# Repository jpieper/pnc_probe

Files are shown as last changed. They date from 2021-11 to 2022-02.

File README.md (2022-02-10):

# Pocket NC Probe Support #

This repository contains:

* Hardware designs to integrate a https://vers.by touch probe into the Pocket NC, https://pocketnc.com
* g-code routines for performing probe operations on the Pocket NC

# Usage #

When installed, [G38.x gcode commands](https://linuxcnc.org/docs/2.6/html/gcode/gcode.html#sec:G38-probe) work as expected.  If the jpieper/pnc_probe subroutines are installed, two new gcode programs are available: `pnc-probe-center-id` and `pnc-probe-center-od`.

These scripts probe features that are close to machine X=0,Y=0 and set G54 to the exact center.

To run either, manually position the probe along either the X axis or Y axis just inside (for ID) or just outside (for OD) at the depth you wish to probe.  Leave sufficient margin (~2mm) so that when the probe checks other directions it will have room to plunge without colliding with the work.

Then start the program.

# Installation #

## Hardware ##

Watch the following video:

TODO

1. Attach the adapter housing to the A axis stepper using a cable tie.  The cable tie should be pulled tight, as this helps keep the enclosure sealed from chips.

2. Disconnect the RJ45 cable from the A axis carriage and connect it to the bottom RJ45 port on the adapter.  The 1ft long ethernet cable should then be connected from the A axis carriage to the top port of the adapter.

3. To insert the probe, the A axis MUST be moved out of the home position.  Note, the machine CANNOT BE HOMED while the probe is inserted, or it will crash.

4. Using a dial indicator, adjust the M2 screws accessed through holes in the front of the probe to reduce runout at the tip of the probe.

5. Remove the screw cap from the adapter enclosure, attach the probe cable to the USB port.  Note, this is not actual USB, but that is the cable the vers.by ships with.

6. Attach the magnetic coupled end of the cable to the probe.

7. When removing the probe, be sure to reinstall the USB cap, otherwise chips may fall into the connector.

## Software ##

1. Copy the contents of the `ncfiles/` and `subroutines/` directories to `/home/pocketnc` on the pocketnc.  You can use WinSCP from Windows, or rsync from Mac/Linux.  A suitable command for linux might look like:

```
rsync -Pv ncfiles subroutines pocketnc@192.168.6.2:
```

2. Depending upon your machine version, you may need to add a .ini overlay.

### Kinetic ###

Modern versions of the Kinetic interface require no changes.

### Kinetic (pre 5.1.2) ###

Older versions of Kinetic require the following overlay added.

 * Config Tab
 * Server
 * INI OVERLAY
 * EDIT OVERLAY (bottom right)
 * If RS274NGC is not already in the list of groups, use the '+' button to add it.
 * Ensure the following key is set as follows:

```
SUBROUTINE_PATH=/opt/pocketnc/Settings/subroutines:/home/pocketnc/subroutines
```

 * If you had to change anything, click "REBOOT MACHINE".

### Legacy ###

TODO

# LICENSE #

All files contained in this repository are available under an Apache 2.0 License: https://www.apache.org/licenses/LICENSE-2.0

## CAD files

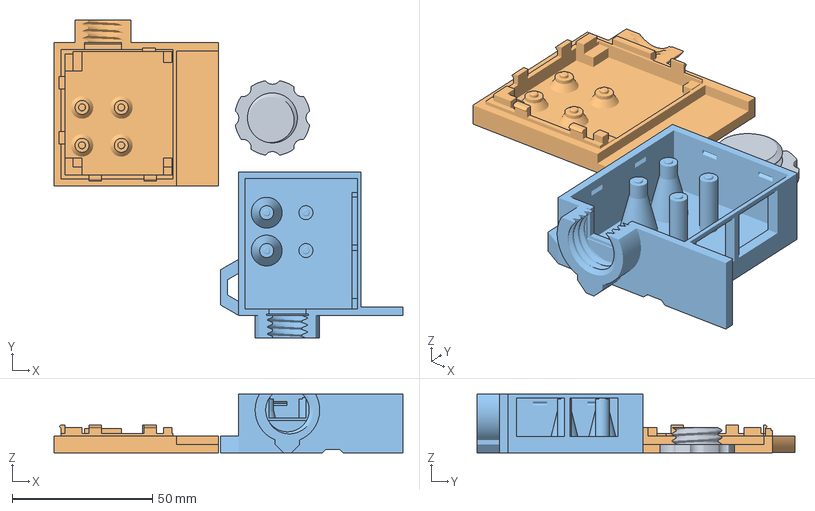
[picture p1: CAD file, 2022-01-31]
enclosure/pnc_probe_enclosure.3mf
124.4 x 113.3 x 21.0 mm
pnc_probe_usb_cap.stl
pnc_probe_enclosure_bottom.stl
pnc_probe_encosure_top.stl

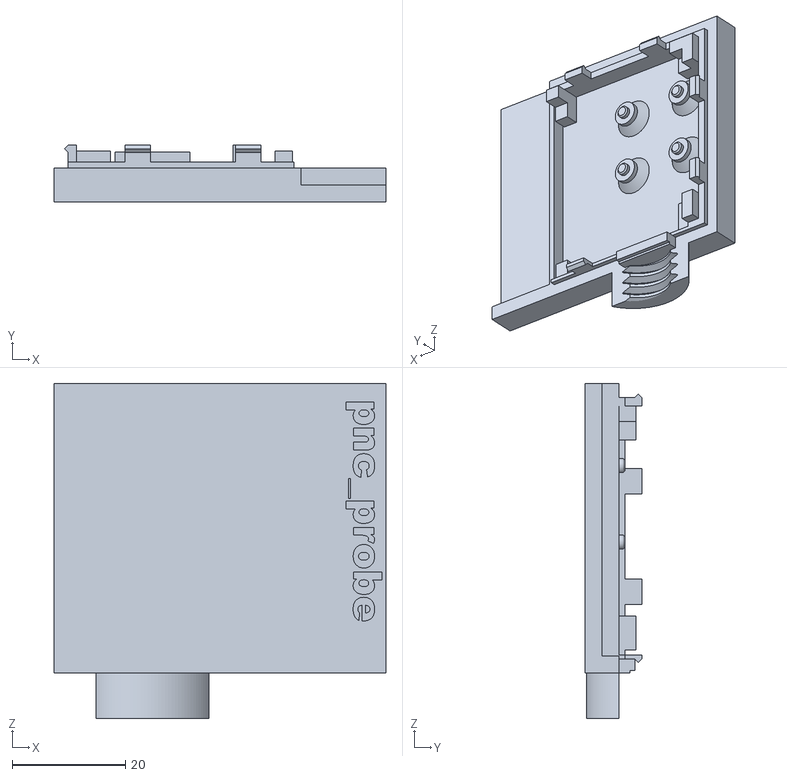
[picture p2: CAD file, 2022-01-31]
enclosure/pnc_probe_enclosure_bottom.stl
58.6 x 10.0 x 59.1

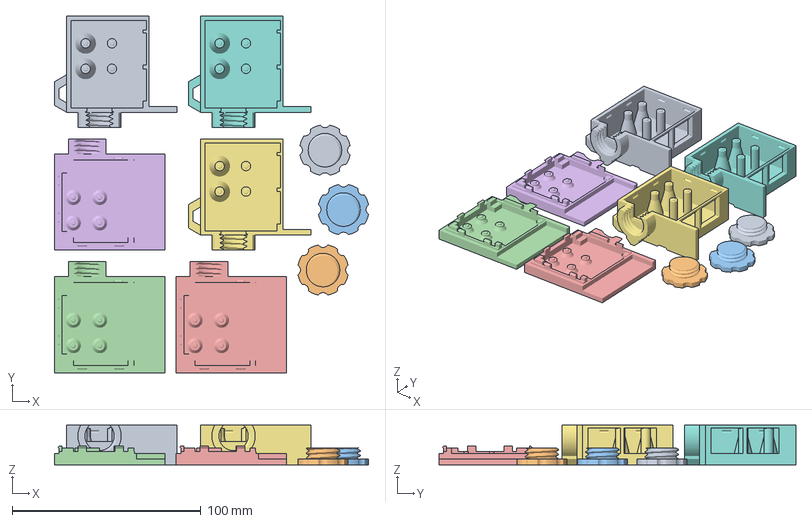
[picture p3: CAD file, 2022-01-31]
enclosure/pnc_probe_enclosure_3x_array.3mf
166.6 x 189.4 x 21.0 mm
pnc_probe_usb_cap.stl
pnc_probe_enclosure_bottom.stl
pnc_probe_encosure_top.stl

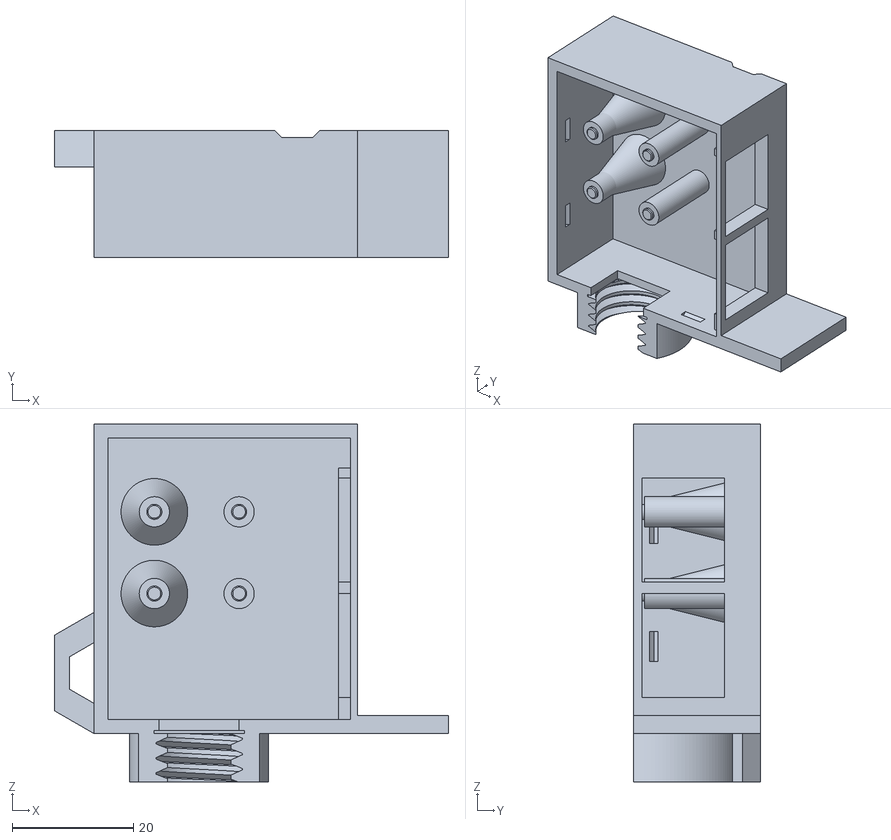
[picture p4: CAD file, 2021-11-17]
enclosure/pnc_probe_enclosure_top.stl
65.1 x 21.0 x 59.1

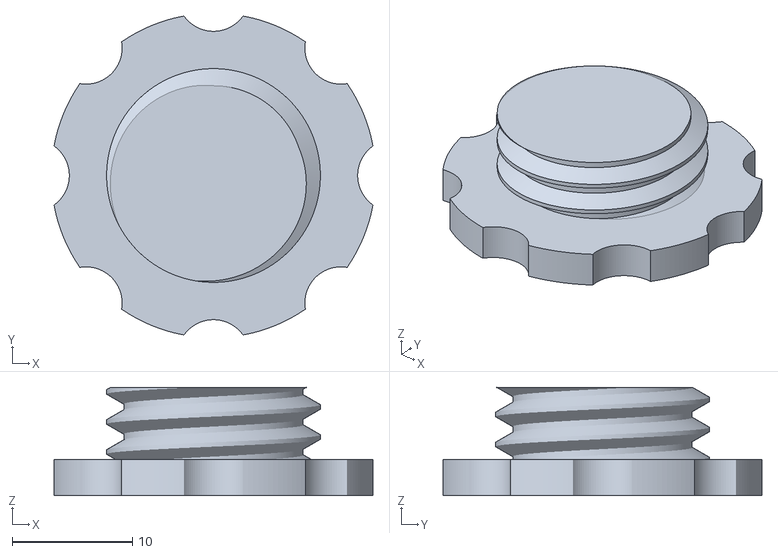
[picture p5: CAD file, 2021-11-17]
enclosure/pnc_probe_usb_cap.stl
26.6 x 26.6 x 9.00

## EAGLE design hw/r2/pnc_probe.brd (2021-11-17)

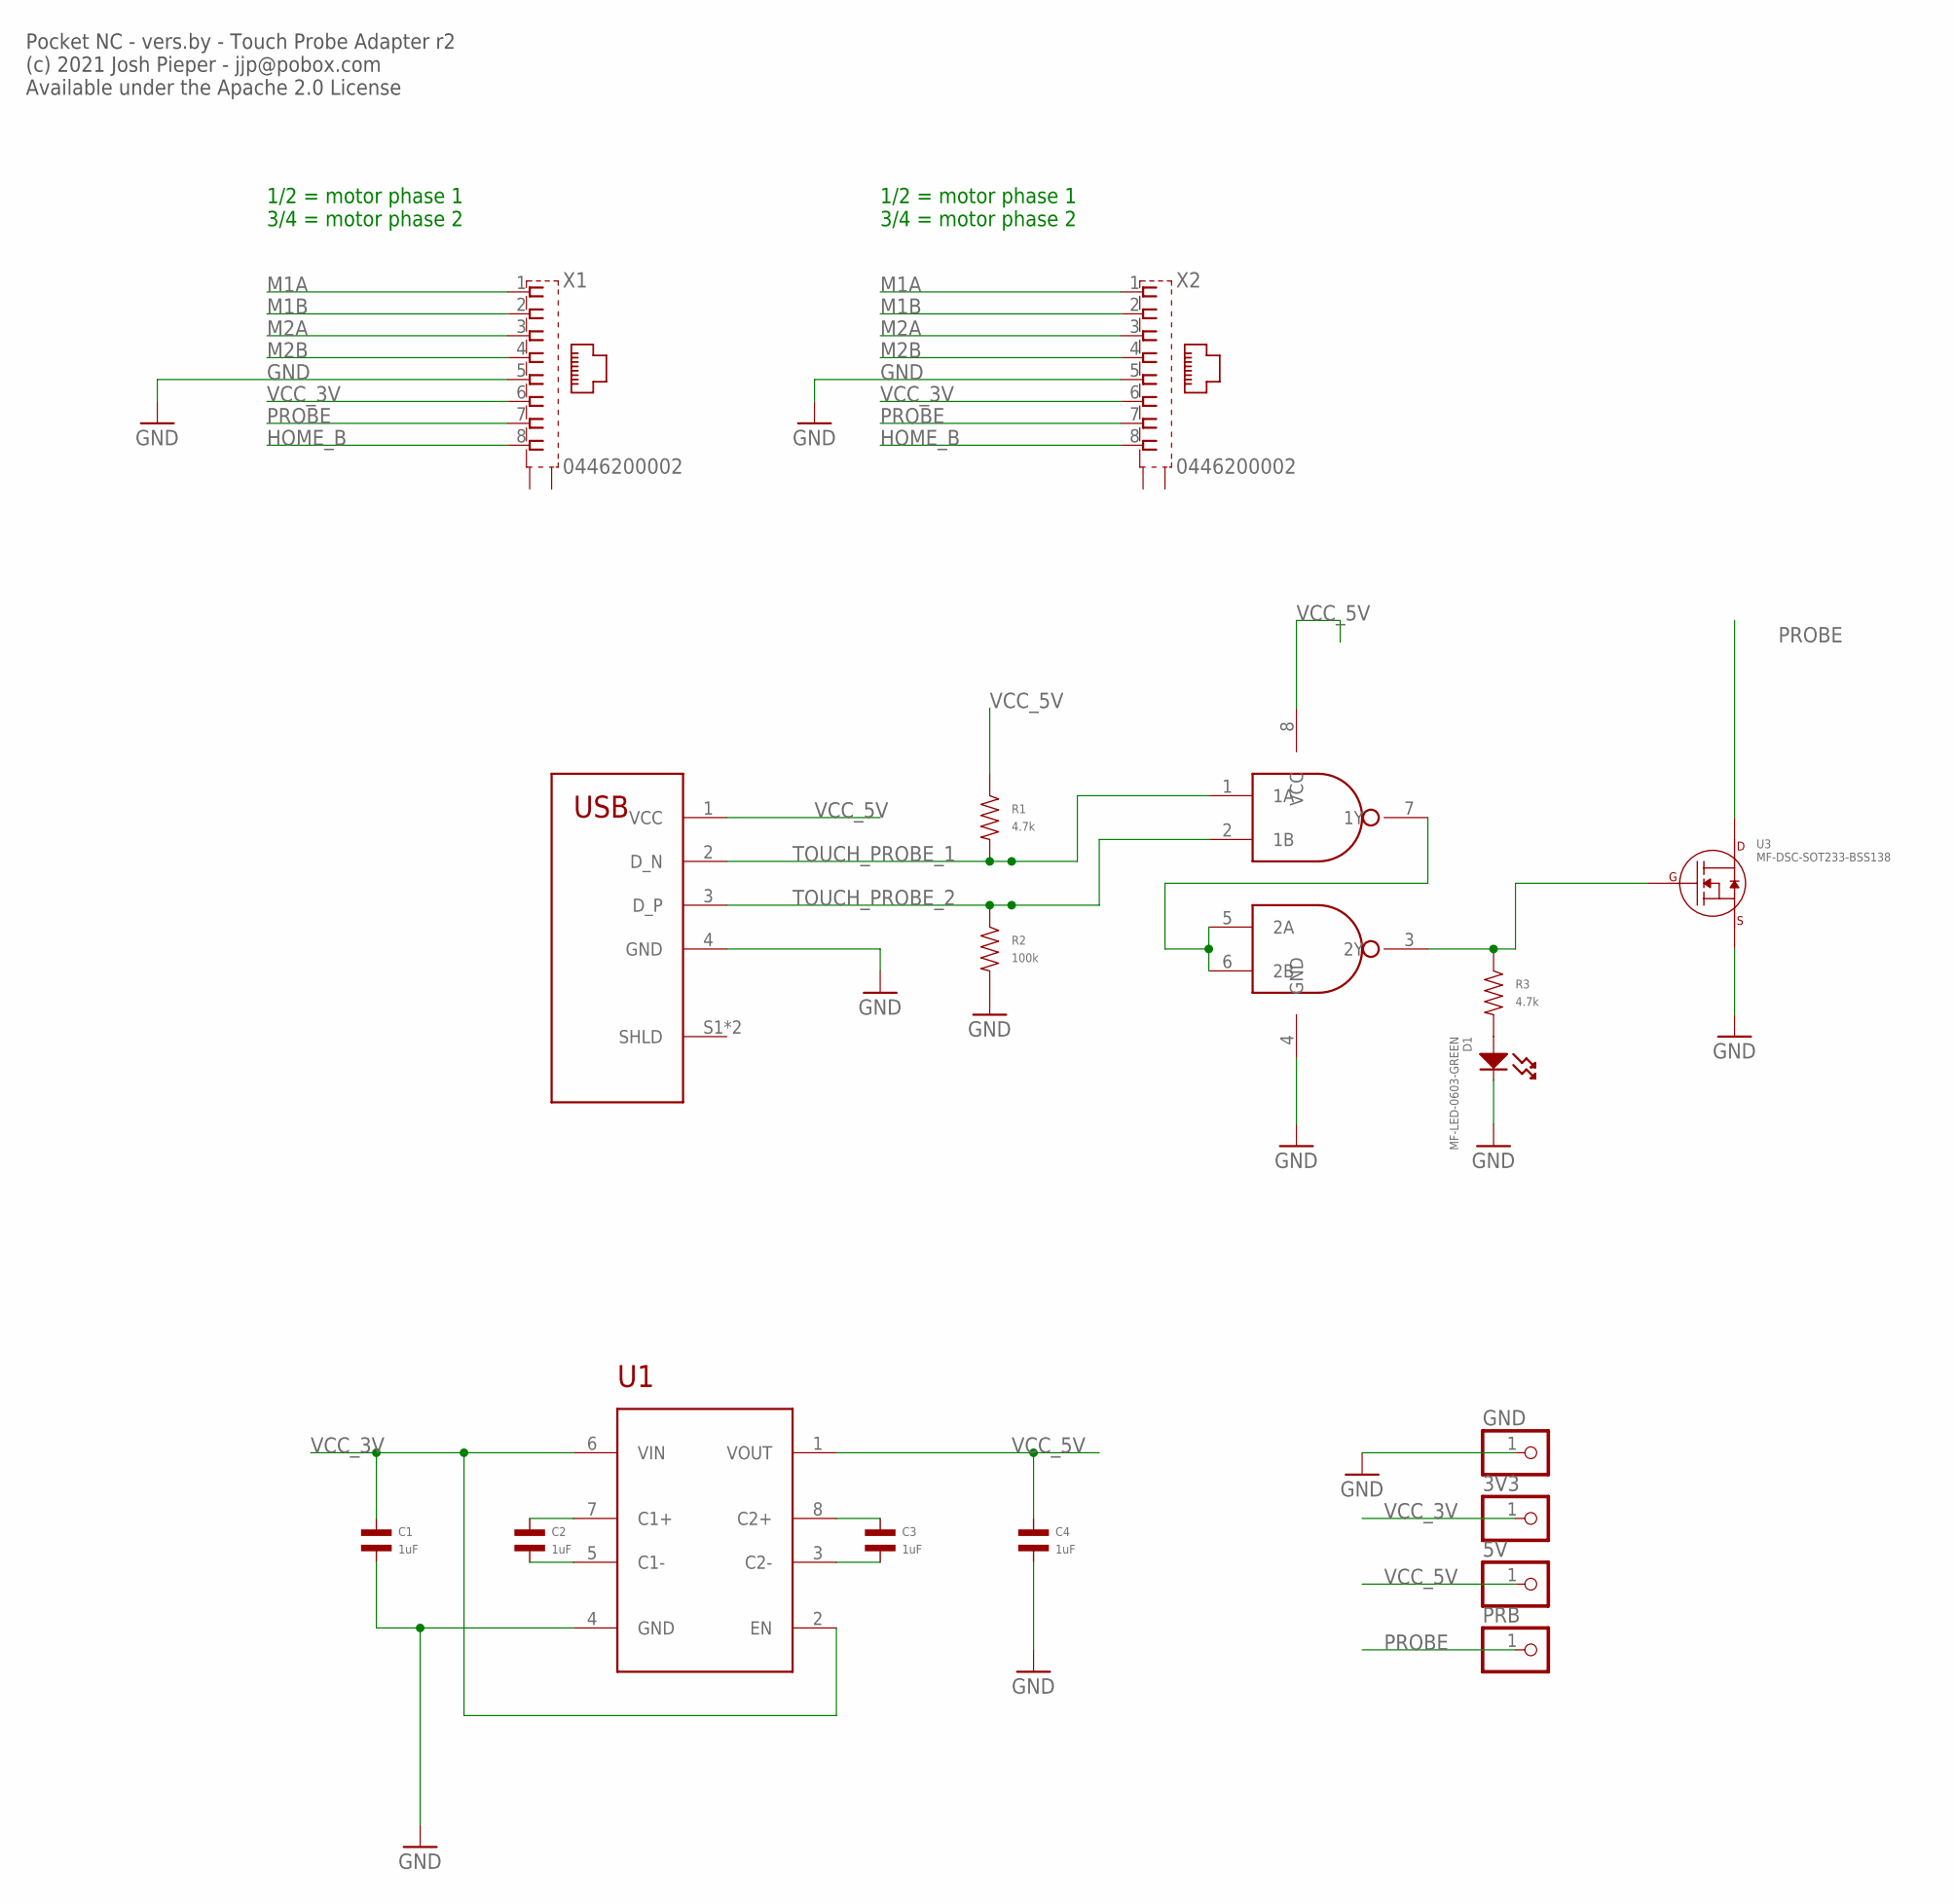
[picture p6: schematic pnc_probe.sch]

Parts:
3V3, 5V: PINHD-1X1; 1X01
C1, C2, C3, C4: 1uF; C0603; MPN MF-CAP-0603-1uF
D1: MF-LED-0603-GREEN; LED0603
GND: PINHD-1X1; 1X01
PRB: PINHD-1X1; 1X01
R1, R3: 4.7k; R0603; MPN MF-RES-0603-4.7K
R2: 100k; R0603; MPN MF-RES-0603-100K
U1: TPS6024X_VSSOP8; VSSOP8
U2: DUAL_NAND_SSOP8; SSOP8; MPN SN74LVC2G00DCTR
U3: MF-DSC-SOT233-BSS138; SOT-23-3
U$1: USBAUSBA; ONSHORE_USBA_1HSXX
X1, X2: 0446200002

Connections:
GND: C1.P$2, C4.P$2, D1.CATHODE, GND.1, R2.P$2, U1.4 (GND), U2.4 (GND), U3.P$2 (SOURCE), U$1.4 (GND), X1.5, X2.5
HOME_B: X1.8, X2.8
M1A: X1.1, X2.1
M1B: X1.2, X2.2
M2A: X1.3, X2.3
M2B: X1.4, X2.4
unnamed: U2.5 (2A), U2.6 (2B), U2.7 (1Y)
unnamed: C2.P$1, U1.7 (C1+)
unnamed: D1.ANODE, R3.P$2
unnamed: R3.P$1, U2.3 (2Y), U3.P$1 (GATE)
unnamed: C2.P$2, U1.5 (C1-)
unnamed: C3.P$1, U1.8 (C2+)
unnamed: C3.P$2, U1.3 (C2-)
PROBE: PRB.1, U3.P$3 (DRAIN), X1.7, X2.7
TOUCH_PROBE_1: R1.P$2, U2.1 (1A), U$1.2 (D_N)
TOUCH_PROBE_2: R2.P$1, U2.2 (1B), U$1.3 (D_P)
VCC_3V: 3V3.1, C1.P$1, U1.2 (EN), U1.6 (VIN), X1.6, X2.6
VCC_5V: 5V.1, C4.P$1, R1.P$1, U1.1 (VOUT), U2.8 (VCC), U$1.1 (VCC)

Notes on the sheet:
1/2 = motor phase 1 3/4 = motor phase 2
Pocket NC - vers.by - Touch Probe Adapter r2 (c) 2021 Josh Pieper - jjp@pobox.com Available under the Apache 2.0 License

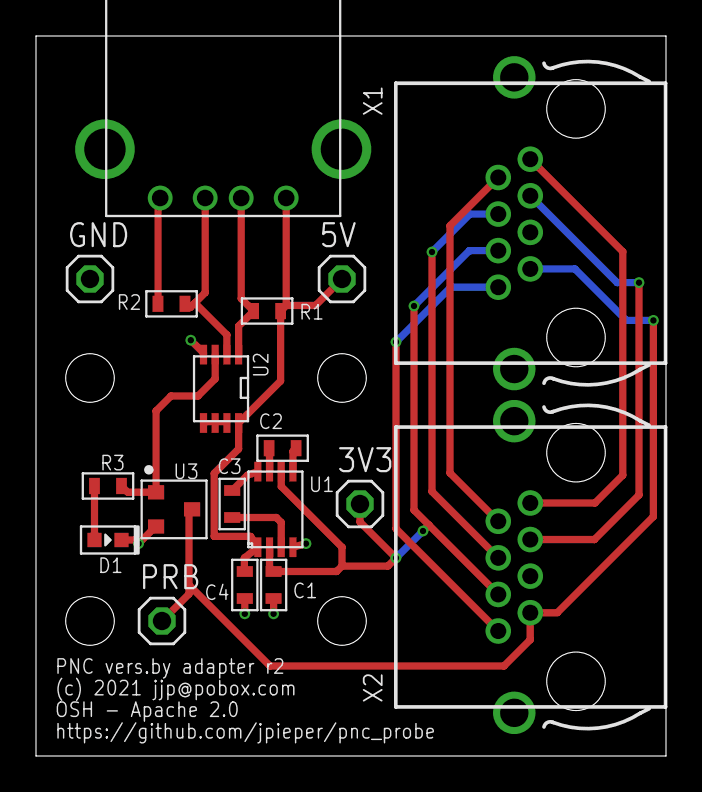
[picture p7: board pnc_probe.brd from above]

Board: 2 copper layers, 35.0 x 40.0 mm, 18 parts (0 on the bottom side), 18 nets.

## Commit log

2021-08-07 Draft of PCB
    [pnc_probe.brd, pnc_probe.sch]
2021-08-07 Random enclosure STLs
    [bottom.stl, enclosure.3mf, front.stl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]
2021-09-23 A script which probes the OD of a circle or square roughly already centered
2021-09-23 Fix r1 errata
    * The footprint for the TPS6024 was wrong. I wasn't able to find a
    sample one, so used a generic VSSOP originally, but that didn't
    match the TI part. I instead used rough dimensions from a KiCAD
    model and double checked against the datasheet.
    * Yikes, I had left some airwires!
    * Added test points for gnd, power, and the final probe signal.
    [pnc_probe.brd, pnc_probe.sch]
2021-09-27 Make an ID as well as an OD probe, from the same basic routine
2021-11-17 Fix a component value
    [pnc_probe.brd, pnc_probe.sch]
2021-11-17 More attempts at an enclosure
    [pnc_probe_enclosure.3mf, pnc_probe_enclosure_bottom.stl, pnc_probe_enclosure_front.stl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]
2021-12-31 r2 as manufactured
    [pnc_probe.brd, pnc_probe.sch]
2022-01-31 Just include production enclosure 3D prints
    [bottom.stl, enclosure.3mf, front.stl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]
2022-01-31 Pull probe offset compensation from config

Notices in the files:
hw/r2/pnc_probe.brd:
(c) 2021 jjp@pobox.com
